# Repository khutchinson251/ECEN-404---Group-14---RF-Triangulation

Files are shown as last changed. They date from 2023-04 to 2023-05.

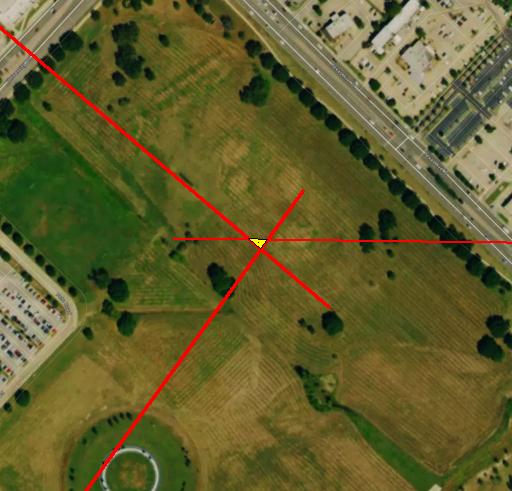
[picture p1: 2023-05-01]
gui/background.jpg

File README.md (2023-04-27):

# ECEN-404-Group-14-RF-Triangulation
ECEN 404 GitHub Repository 

This is for the Texas A&M University Senior Design Class, ECEN 404.
Group 14, RF Triangulation

Our project is based on radio frequency triangulation, where there are three receiving antennas finding one transmitting antenna.
Transmitter have a PCB with a MCU and Radio Module.
Receivers have a PCB with a MCU, Radio Module, and Stepper Motor IC; Stepper Motor; and a 12V battery.

This GitHub will compile all presentations, code, parts, Altium designs, and documentation for the project.

To see the GitHub Repository from ECEN 403, click here: https://github.com/Brandonstokes6/RF-Triangulation

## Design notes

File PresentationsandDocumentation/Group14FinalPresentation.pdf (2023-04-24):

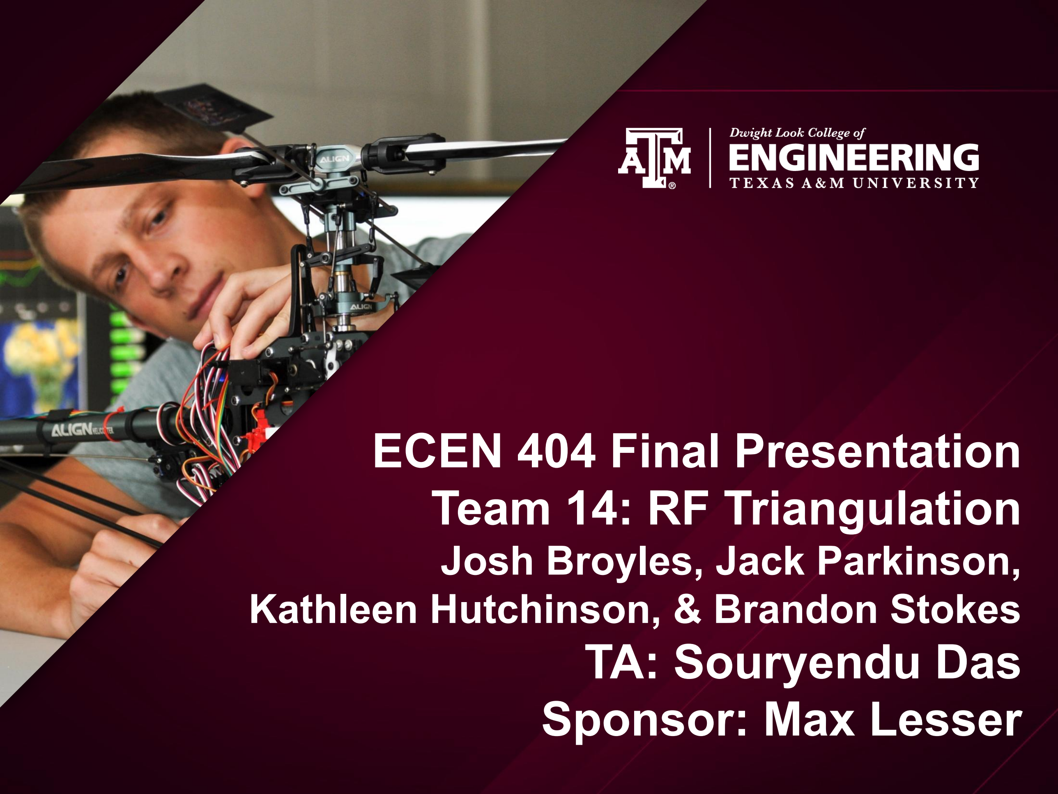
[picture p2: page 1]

# ECEN 404 Final Presentation Team 14: RF Triangulation

Josh Broyles, Jack Parkinson,

## Kathleen Hutchinson, & Brandon Stokes

# TA: Souryendu Das Sponsor: Max Lesser

# Project Summary

Biologists have struggled being able to collect data on wildlife’s location, habitat use, and breeding patterns without getting directly involved with the animal they’re tracking.
Radio Frequency Triangulation
allows a user to track a known
frequency (such as a previously tagged animal) within the
triangulated area of three antennas by using a motor to successfully pinpoint the
strongest signal.

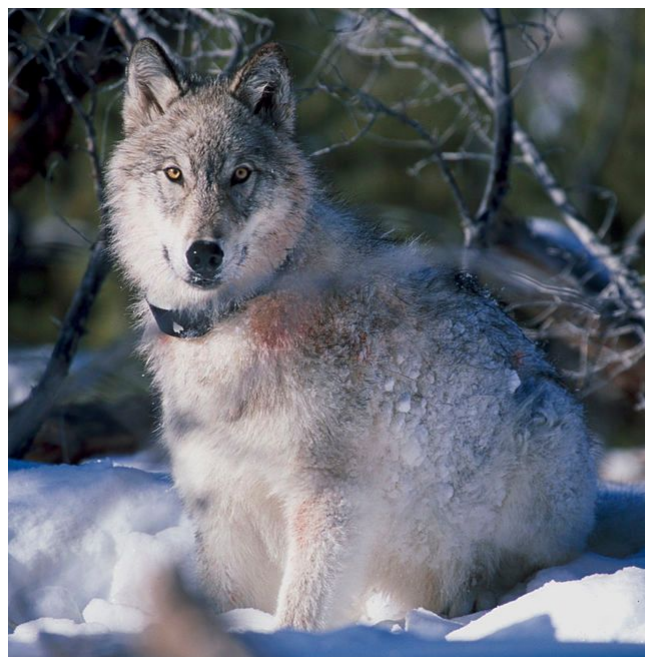
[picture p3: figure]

Helpful to study both invasive and threatened wildlife, our RF Triangulation system will focus on being able to accurately track a transmitter within a 100 meter radius with >10% error.

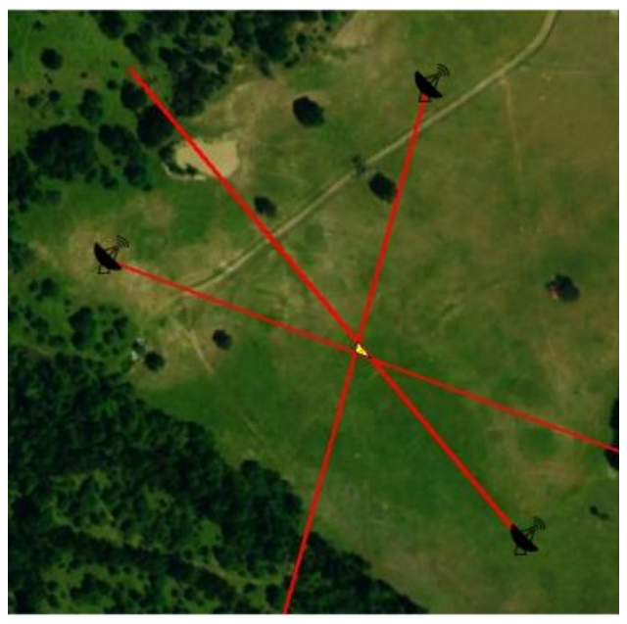
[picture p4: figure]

## Integrated Project Diagram

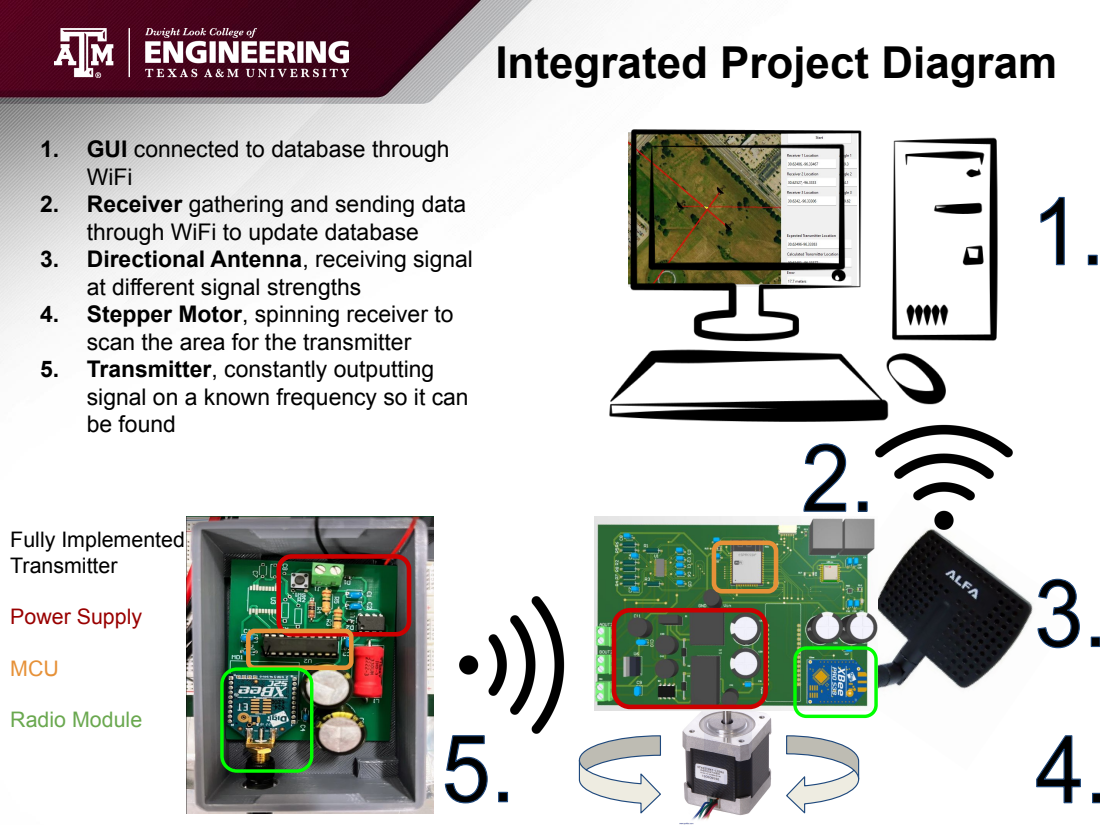
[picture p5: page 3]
Fully Implemented Transmitter; Power Supply; MCU; Radio Module

1. GUI connected to database through
WiFi
2. Receiver gathering and sending data
through WiFi to update database
3. Directional Antenna, receiving signal
at different signal strengths
4. Stepper Motor, spinning receiver to
scan the area for the transmitter
5. Transmitter, constantly outputting
signal on a known frequency so it can
be found

## Josh Broyles Accomplishments

Designed | Tested | Challenges | Solutions

PCB Designed:
- MSP430
- Xbee
- Ublox

Coded
- MSP430
- Transmit
- Echo
- Xbee

PCB:
- Power Supply
- Line Regulation
- Load Regulation

Code:
- MSP430 Transmit
message to Xbee
- MSP430 Echo
message back
through Xbee

Other:
- Transmitter
Range Test
- MSP430
unresponsive I2C
commands
- MSP430
debugging without
terminal
- MSP430 reset
does not rerun
program
- GPS
coordinates can
be hardcoded in
- MSP can output
messages to
Xbee, which can
be used to
debug
- Turning the
system off then
back on will
rerun the
program

## Josh Broyles Designed / Coded

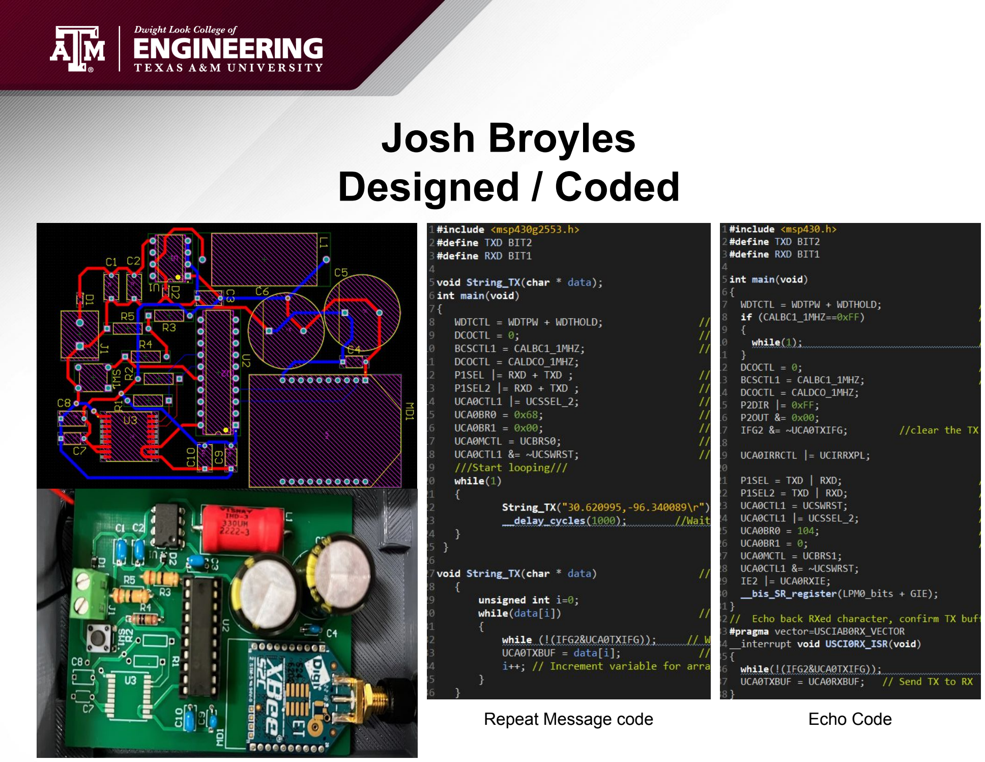
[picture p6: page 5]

Repeat Message code | Echo Code

## Josh Broyles Validation

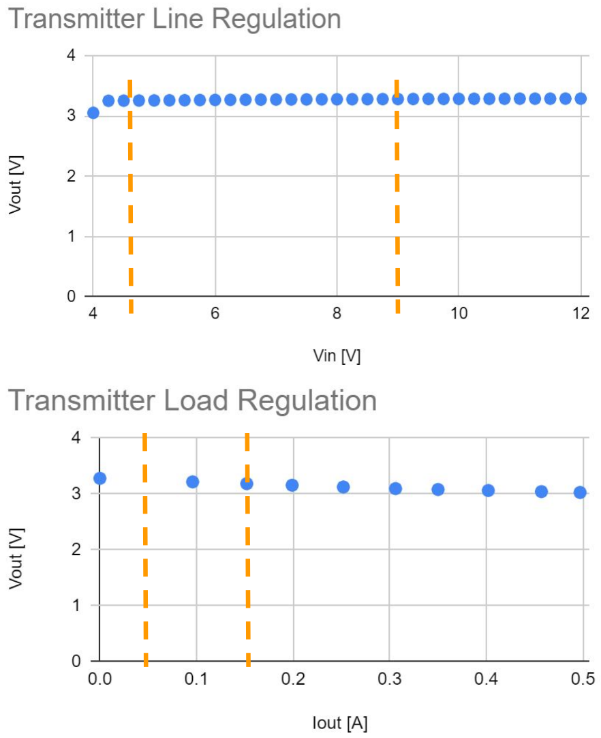
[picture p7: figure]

Requirement | Validated
Vout = 3V - 3.3V with Vin between 4.5V - 9V | Vin = 9V, Vout = 3.281V Vin = 4.5V, Vout = 3.25V
3V - 3.3V at 0.15A for MCU and other modules | 3.182V at 0.152A

## Jack Parkinson Accomplishments

Designed | Tested | Challenges | Solutions

PCB Design:
- Stepper Motor
Driver
- 12V regulator

Directional Antenna:
- Patch Antenna
- Yagi Antenna

ESP32 Stepper
Motor Code

PCB:
- 12V regulator

Directional Antenna:
- directionality
- range

Stepper Motor:
- speed
- step size
- step direction
- motor torque
- ESP32 flash
capabilities
- Motor Driver
parts too small
- 12V regulator
dropout voltage
too large
- Patch Antenna
simulation
- Yagi antenna
manufacturing
- Redesign
PCB
- Buy new parts
- Buy an
antenna

## Jack Parkinson Tested

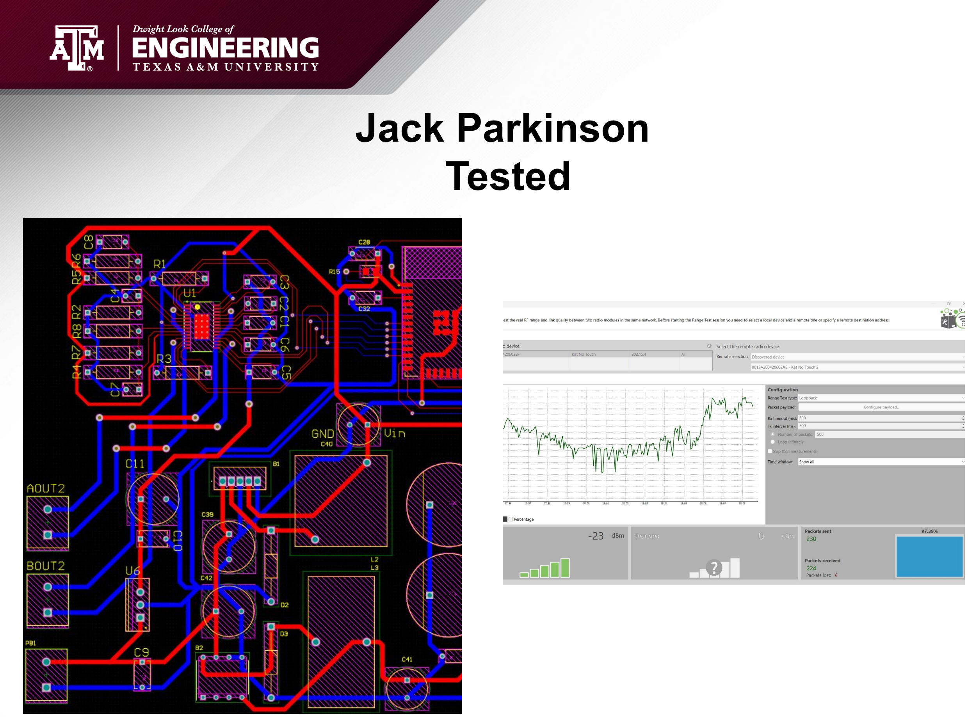
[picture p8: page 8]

## Kathleen Hutchinson Accomplishments

Designed | Tested | Challenges | Solutions

PCB Designed:
- ESP32
- XBee
- GPS
- Magnetometer
- Pycom

Coded
- ESP32
- XBee
- Pycom

PCB:
- Power Supply
- ESP32 Tx0/Rx0

Code:
- ESP32 reading
XBee data
- ESP32 reading
and transmitting
Pycom data
Other:
- XBee Accuracy
- Transmission Time
- SPI and I2C with
small, surface
mount modules
- Circuit/PCB
design
- XBee RSSI value
- XBee accuracy
(packets) drop
after 50 meters
- Power Supply
(inductors,
heating problems)

GPS Coordinates
can be manually
set since phone
hotspots will be
used

Power supply and
connections are
updated on new
PCB

## Kathleen Hutchinson Designed / Coded

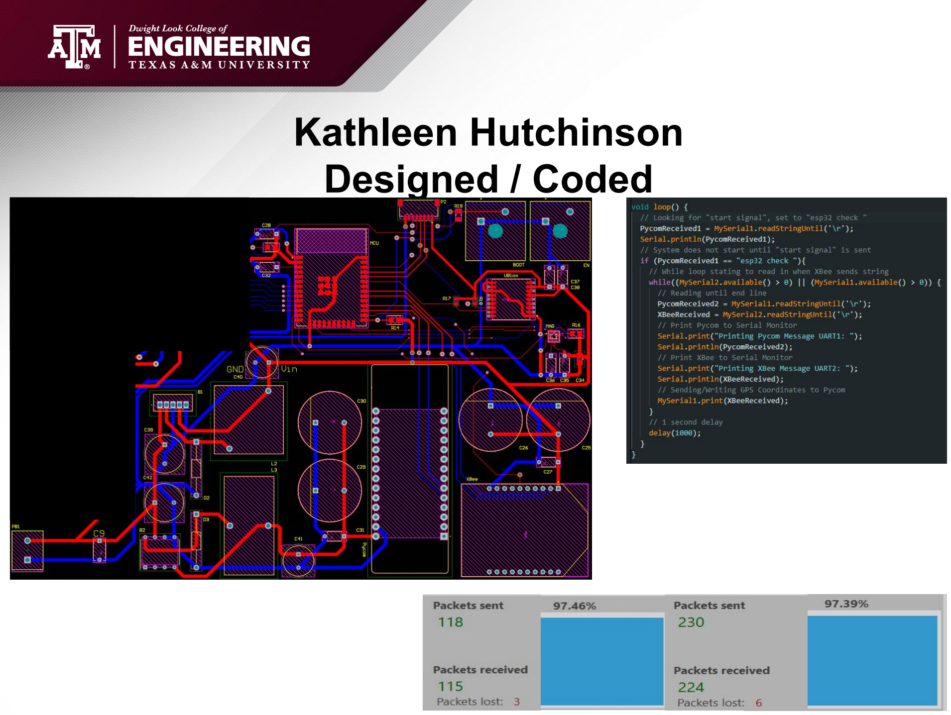
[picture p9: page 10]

## Kathleen Hutchinson Validation

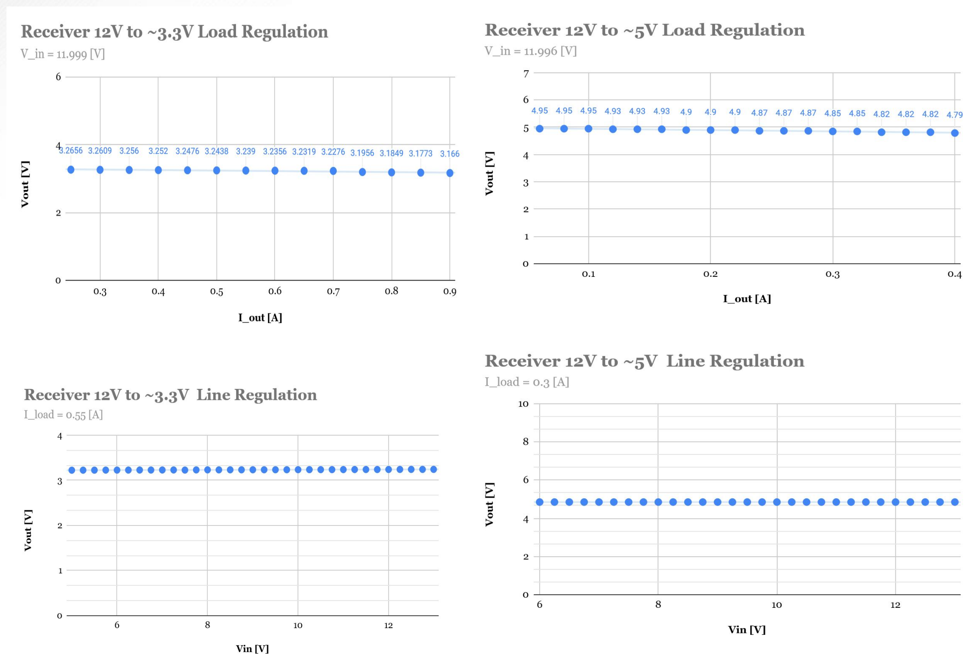
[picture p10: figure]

Requirement | Validated
3V at 1A for modules & MCU | 3.1V at 1A
3.5V at 0.5A for Pycom | 4.7V at 0.5A
30 sec transmission time | ~14 sec transmission time

## Brandon Stokes Accomplishments

Designed | Tested | Challenges | Solutions

GUI Designed:
- Display locations
based on GPS
- Satellite map view
of the area
- Error between the
calculated and
actual transmitter
Database:
- Hosted on AWS that
stores all the
relevant information
Pycom:
- Coded communication
between GUI,
Database and MCU

WiFi:
- WiFi connection
will be able to run
continuously for 20
minutes and be
able to reconnect
Code:
- Gives errors for wrong
values(i.e given a
wrong angle will tell
you which receiver it
came from
- How much RAM the
program takes up on
Users computer
Other:
- Database integrity
to not allow
duplicate values for
receiver data
- LTE | Solution to not having LTE was to use WiFi hotspots as the connection for each of the receivers

## Brandon Stokes Design

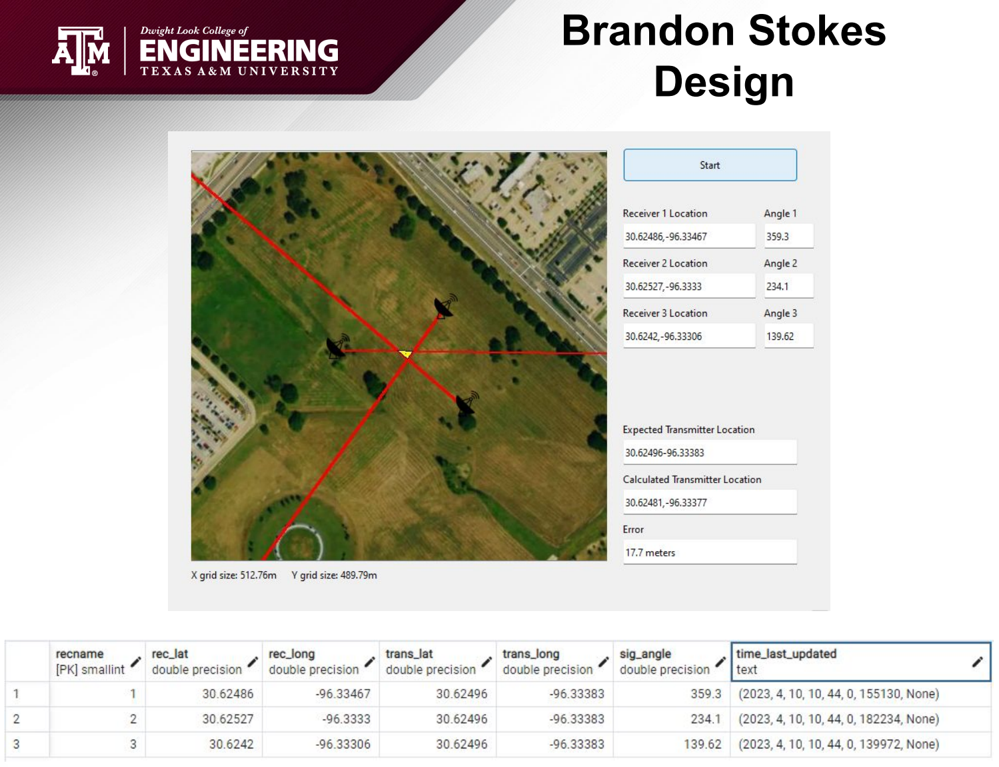
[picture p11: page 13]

## Brandon Stokes Validated

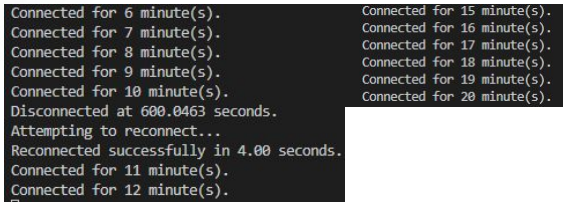
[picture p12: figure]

Requirement

The wifi hotspot does not drop more than 1 time per 5 minutes
and shall reconnect within 20s.

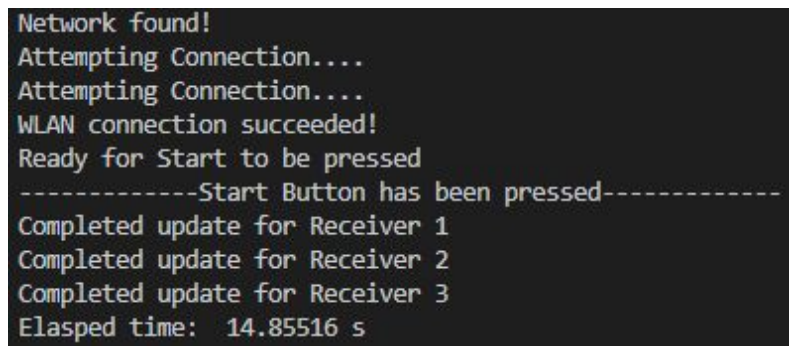
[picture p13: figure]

Total Pycom connection time max = 20 min

The time it takes to connect and transmit data between the GUI, transmitter, and receiver shall be 30s.

The GUI shall not take up more than 1 GB RAM on user's computer.

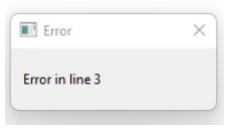
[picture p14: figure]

The Database should not be able to take in duplicate values or
values that do not match the expected criteria

# Integrated System Results

The connection between the transmitting XBEE and the receiver’s XBEE, ESP32, Pycom, to database transmits in about 14 seconds, as previously stated in Brandon Stokes’s slide.

When within about 50 meters of each other, the XBEE’s have an accuracy of 97%; however, our project requires a distance of 100 meters from each antenna - thus an updated antenna is required.

Performance will be improved with a redesigned PCB.

Success in this area was described as successfully transmitting data, failure would be a lack of communication.

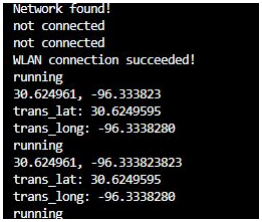
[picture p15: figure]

Further system success criteria requires the motor and redesigned PCB
to successfully move to find the transmitter.

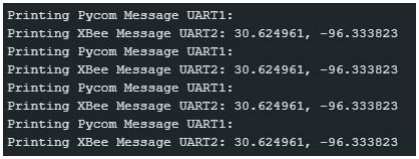
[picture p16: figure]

# Conclusions

Some parts of the project were changed due to changes in the modules. Specifically, the major changes resulted in the project moving from:
- Automatically reading in GPS coordinates from the UBLOX module to | manually
entering the coordinates | because the team was unsuccessful in reading the data.
- Using the magnetometer to move system to North to | manually setting the | receivers
facing North when placed in the field.
- Using LTE through the Pycom module because the module refused to connect with multiple sim cards, thus the team switched to WiFi hotspots.

Current Status

Transmitter | Fully Tested/Validated
Antenna and ESP32+Modules | Repeating Testing for Replacement PCB
Motor and ESP32+Modules | Repeating Testing for Replacement PCB
Pycom and ESP32+Modules | Repeating Testing for Replacement PCB
GUI + Database and Pycom | Fully Integrated/Tested/Validated

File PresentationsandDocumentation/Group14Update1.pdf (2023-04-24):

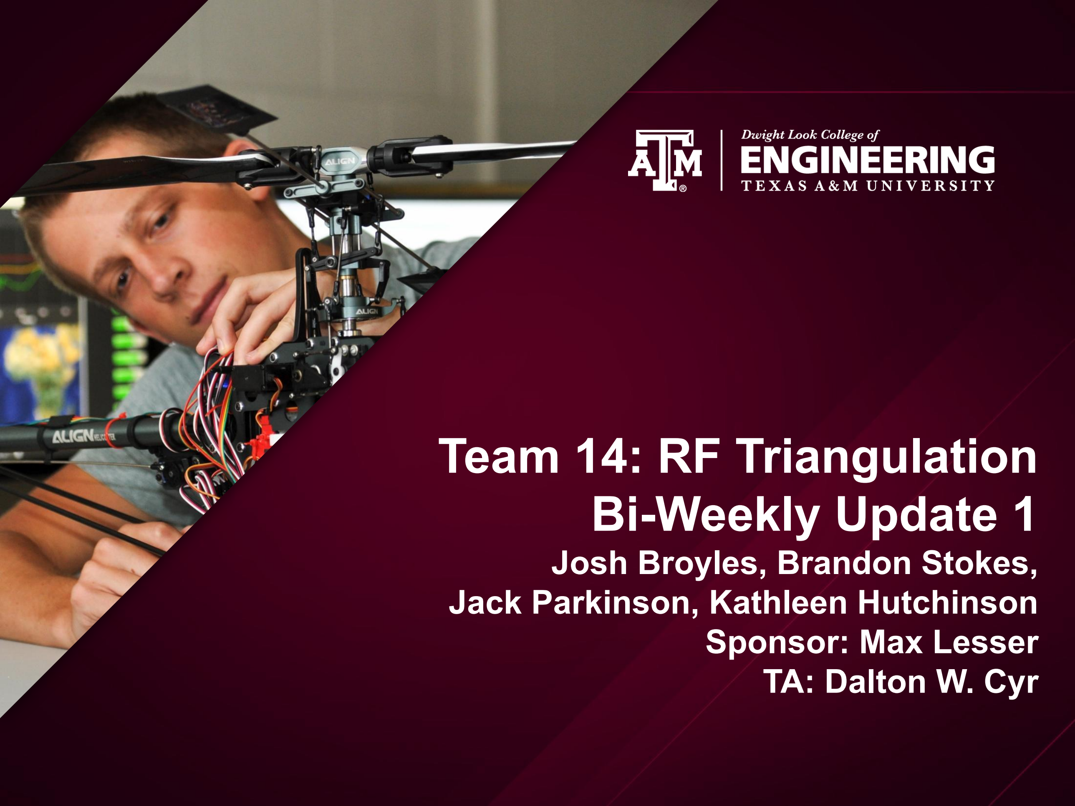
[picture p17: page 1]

# Team 14: RF Triangulation Bi-Weekly Update 1

Josh Broyles, Brandon Stokes,

### Jack Parkinson, Kathleen Hutchinson Sponsor: Max Lesser TA: Dalton W. Cyr

# Project Summary

This project utilizes three receivers with motors to scan an area for the

strongest radio frequency signal from the transmitter and use their

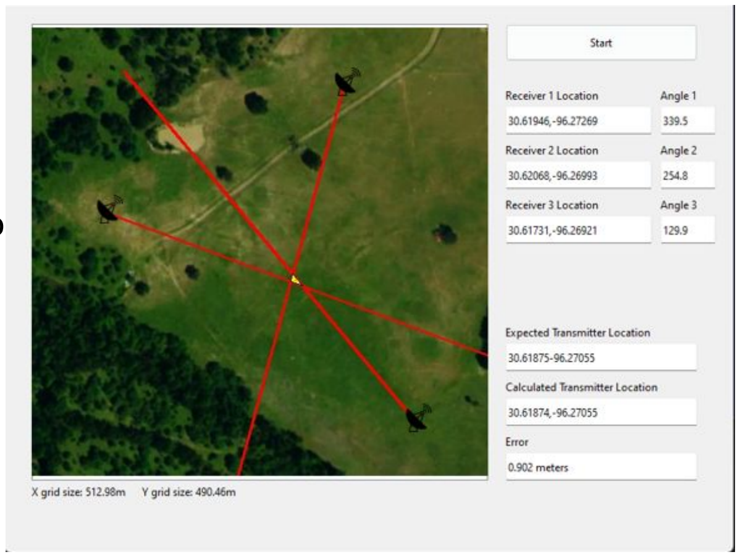
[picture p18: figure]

collective angles from “true” North to determine the location of the transmitter.

Then, the GUI will display this information to the user.

## RF Triangulation deals with determining the random

location of a transmitter in an 100 meter area.

# Project/Subsystem Overview

Josh Broyles - Transmitter
- PCB design for Transmitter
- Programming Transmitter MCU
- Sends out Radio Frequency

Jack P. - Receiver - Antenna/Motor
- PCB design for motor driver
- Programming ESP32 for motor
- Receives signal

Kathleen H. - Receiver - ESP32 Modules
- PCB design for ESP32 and 4 modules
- Programming ESP32 for modules
- Sends signal to Database

Brandon Stokes - Database & GUI
- Database creation
- Display of transmitter location to User
- Error calculation through GPS

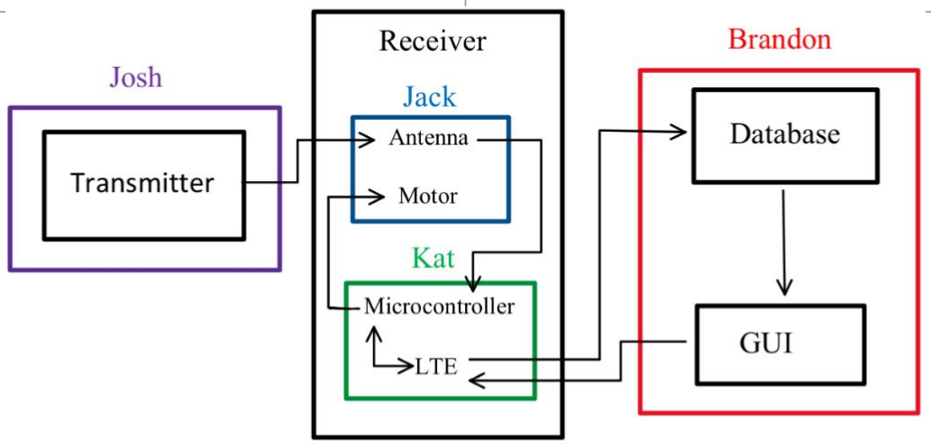
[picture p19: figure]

# Major Project Changes for 404

Original Goal:
Search area of minimum 500 meters
Now:
Due to the higher frequency of the XBEE’s used, the maximum distance will now be 100m

Original Subsystems:
Kathleen had been tasked with programming the Pycom (LTE Module) for the database connection
Now:
Brandon will take over programming the Pycom (LTE Module)

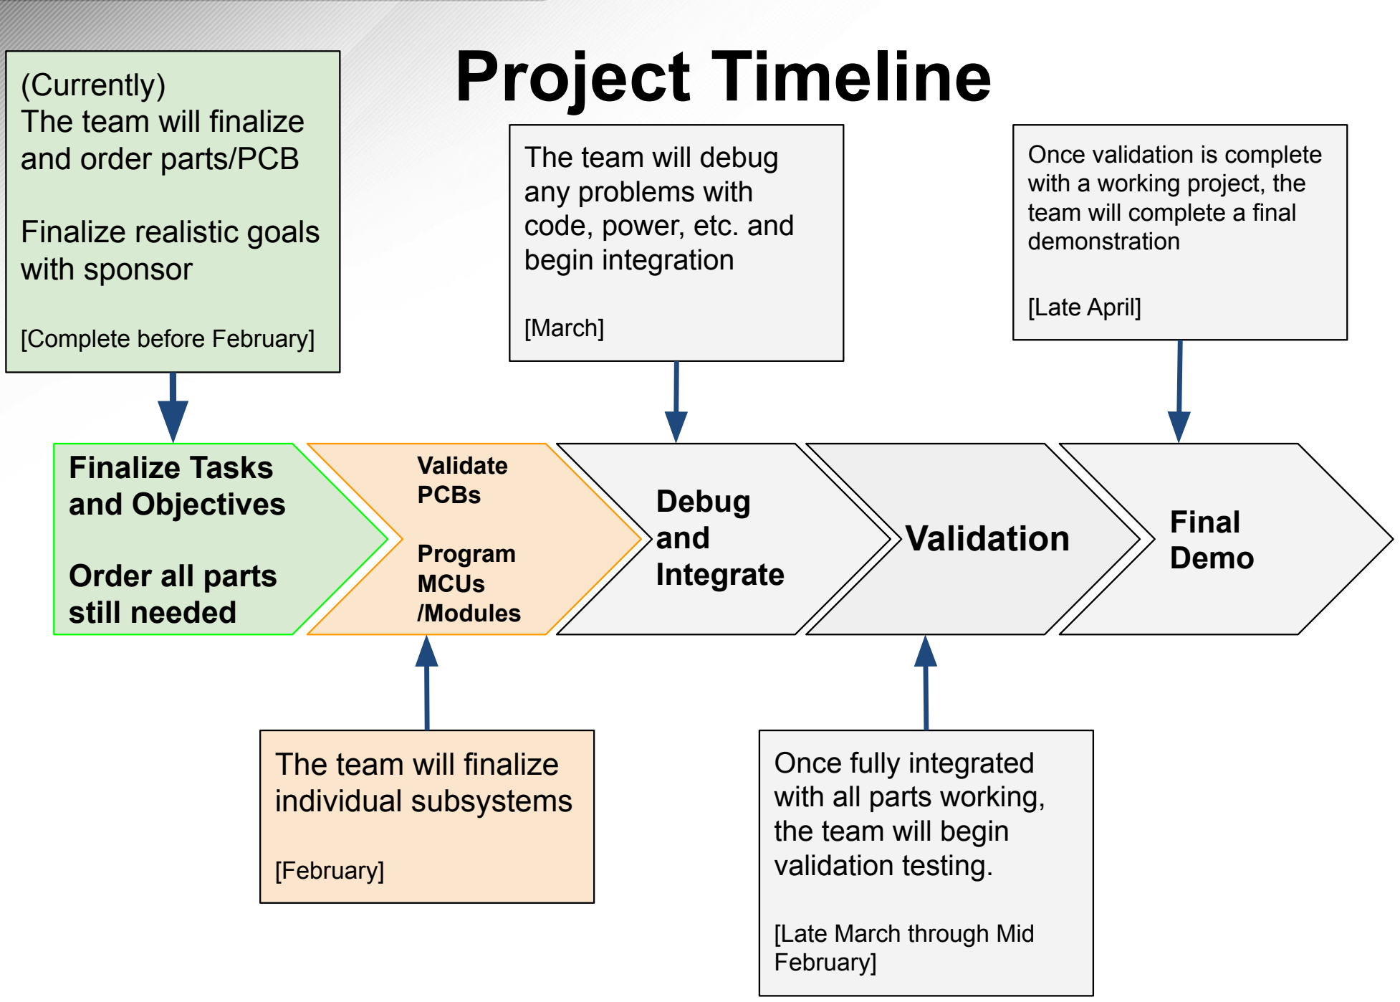
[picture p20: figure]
Project Timeline; Validate PCBs; Program MCUs /Modules; Finalize Tasks and Objectives; Order all parts still needed; Final Demo Validation; Debug and Integrate; (Currently) The team will finalize and order parts/PCB; Finalize realistic goals with sponsor; [Complete before February]; The team will finalize individual subsystems; [February]; The team will debug any problems with code, power, etc. and begin integration; [March]; Once fully integrated with all parts working, the team will begin validation testing.; [Late March through Mid February]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

# Transmitter

Josh Broyles

Accomplishments since 403
14 hrs of effort

Ongoing progress/problems and plans until the next presentation

PCB fabricated

PCB rung out and validated

Radio communication established

Radio distance test (reaches up to 150m)

Set up GPS on PCB

Update MCU code for GPS input

# Transmitter

Josh Broyles

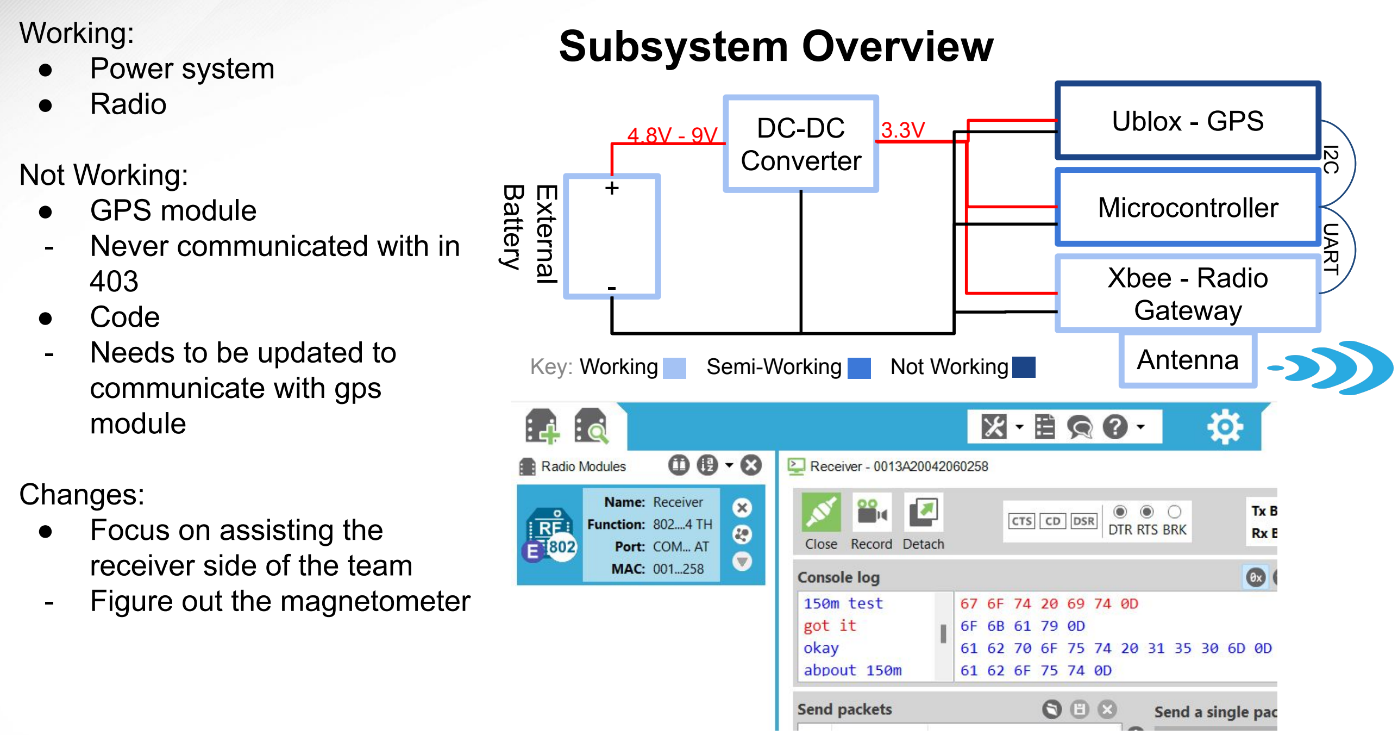
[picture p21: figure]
DC-DC Converter; Battery; External; Ublox - GPS; Microcontroller; Xbee - Radio Gateway; UART I2C; Subsystem Overview; Antenna; Working: ● Power system ● Radio; Not Working: ● GPS module - Never communicated with in 403 ● Code - Needs to be updated to communicate with gps module; Changes: ● Focus on assisting the receiver side of the team - Figure out the magnetometer; Key: Working; Semi-Working; Not Working

# Receiver: Antenna & Motor

Jack Parkinson

Accomplishments since 403
12hrs of Effort

Ongoing progress/problems and plans until the next presentation Made a contingency plan with sponsor for the future of the antenna

1. Working on antenna simulation

and design

2. Helping with PCB finalization
3. Continue working on code to

control the motor

# Receiver: Antenna & Motor

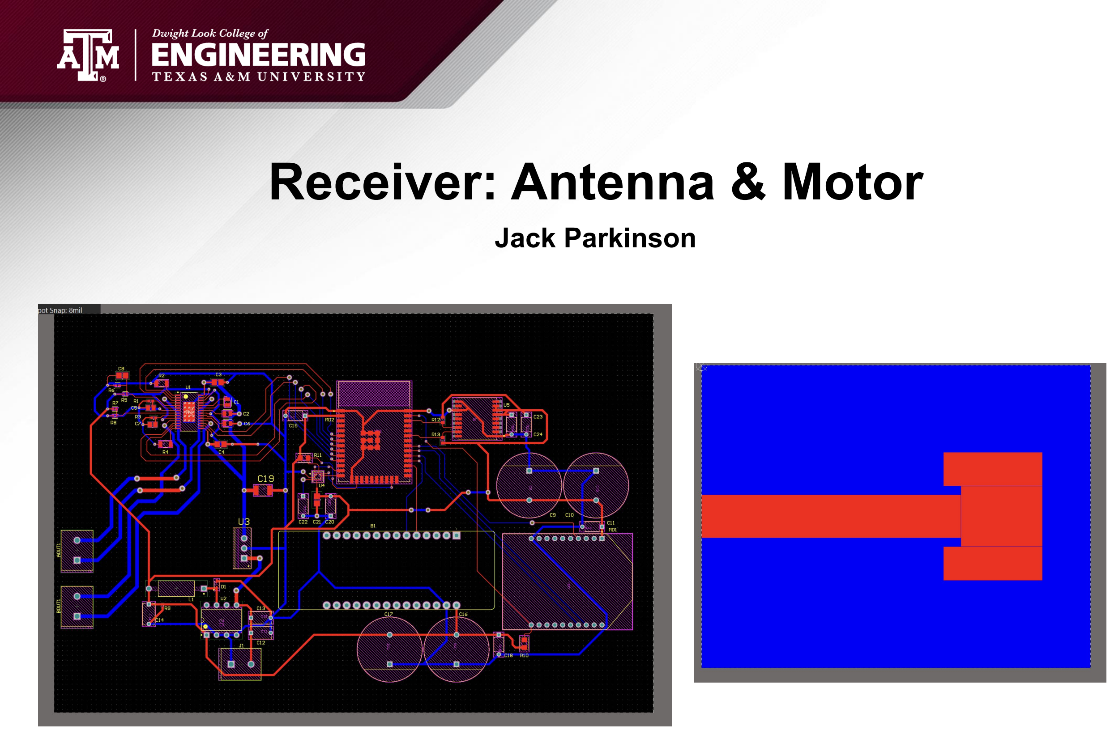
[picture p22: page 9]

Jack Parkinson

Interesting figure related to your subsystem
progress

Detail on what works,
what doesn’t, what is
changing

# Receiver: ESP32 & Modules

Kathleen Hutchinson

Accomplishments since 403
15 hrs of effort

Ongoing progress/problems and plans until the next presentation

Radio distance test (reaches up to 150m)

New Schematic for Receiver
(due to change in PCB Design discussed with Dr. Lusher)
1. PCB Design Finalization &

confirm with Dr. Lusher

2. Order PCB & required parts
3. Continue to program ESP32 for

XBee & verify (while waiting for PCB

to be printed)
4. Work with Brandon on LTE

## Receiver: ESP32 & Modules

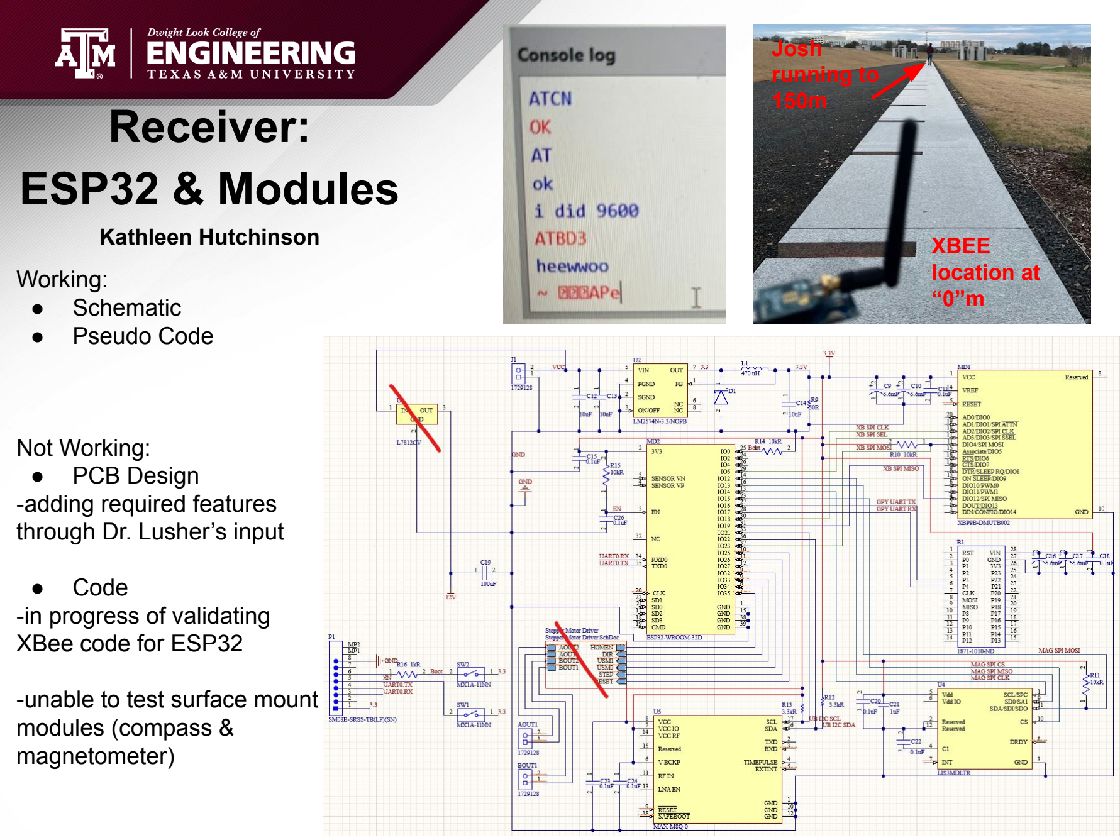
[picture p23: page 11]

Kathleen Hutchinson

Working: ● | Schematic ● | Pseudo Code
Not Working: ● | PCB Design

-adding required features
through Dr. Lusher’s input ● Code

-in progress of validating XBee code for ESP32

-unable to test surface mount modules (compass &
magnetometer)

Josh
running to
150m

XBEE
location at
“0”m

# Database & GUI

Brandon Stokes

Accomplishments since 403
15 hrs of effort

Ongoing progress/problems and plans until the next presentation Added some extra functionality to allow the receivers data to come in at different times

-Data Validation to ensure data is correct before beginning process -Rework the database schema to handle successive runs
-General error checking to pinpoint if one receiver is not incorrect
-Fixing where you do not need to press start again if its outside the bound

# Database & GUI

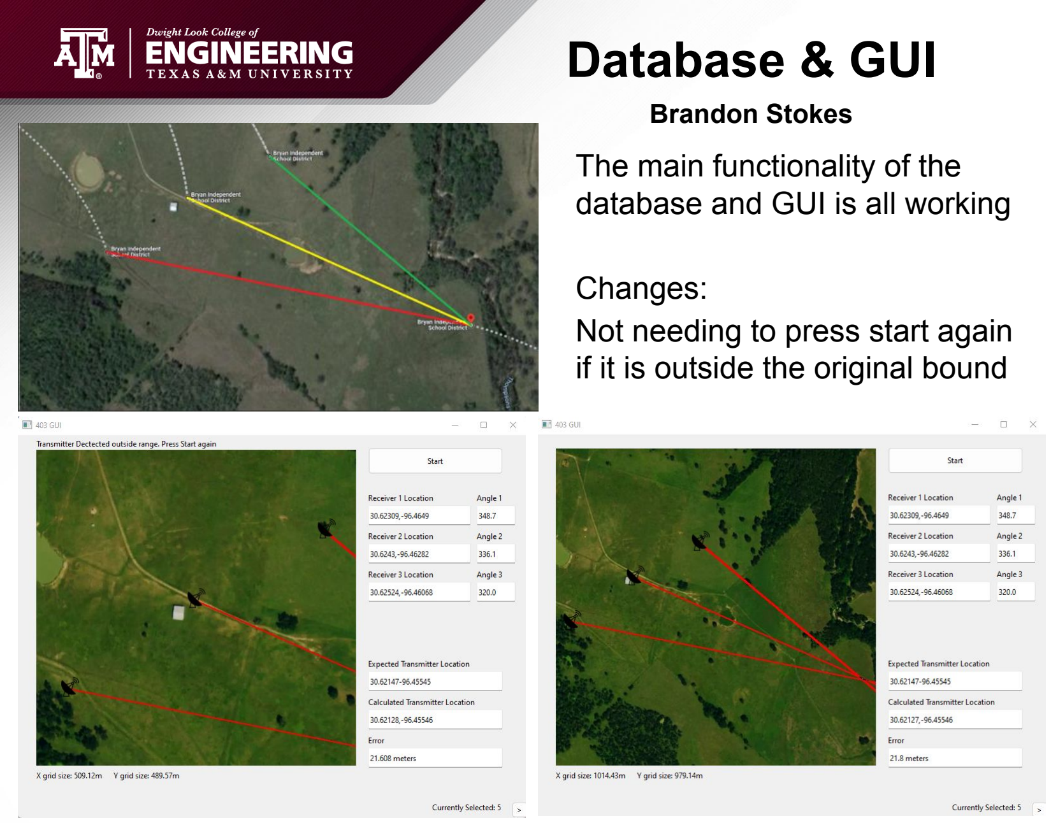
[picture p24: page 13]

The main functionality of the database and GUI is all working

Changes:
Not needing to press start again if it is outside the original bound

Brandon Stokes

# Parts Ordering Status

Transmitter:
- All parts received, including printed PCB

Receiver:
ESP32/Modules
- Informed recently from Dr. Lusher that PCB design was missing parts
- Parts will be ordered within the week:
■ New Inductor
■ More Resistors
■ Push Buttons
■ USB Connector
■ LTE Antenna & Chip
■ Stepper Motor Controller IC
- PCB will be ordered within the week

Antenna:
- Antenna Design is still being worked on but should be ordered by next week

# Execution & Plan

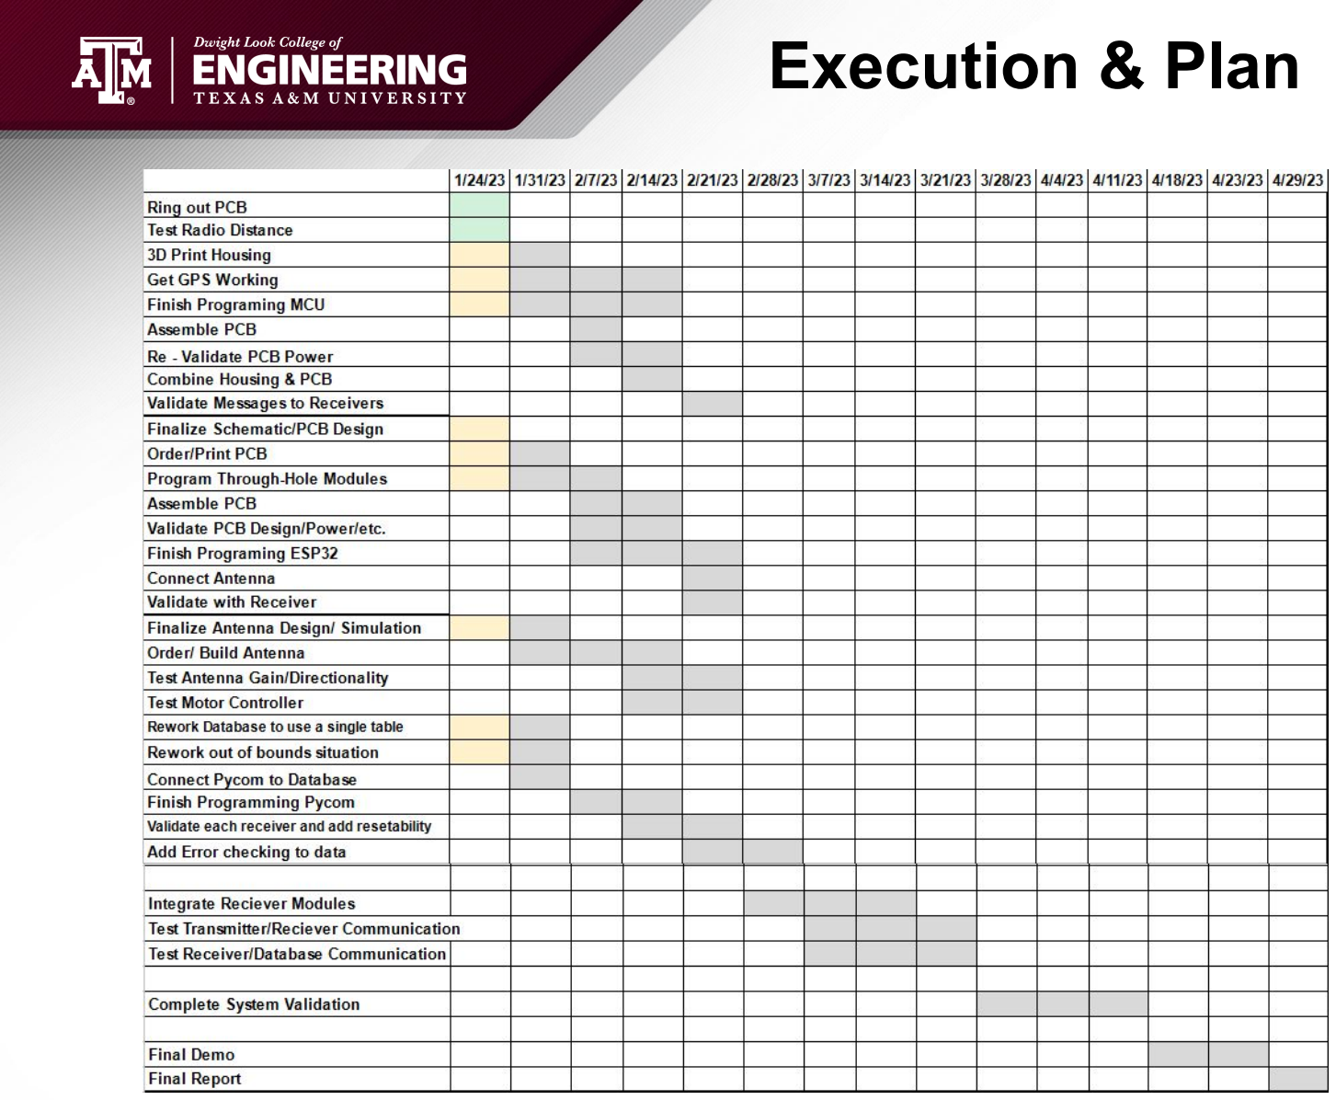
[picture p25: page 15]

# Thank you for your attention!

# Feel free to ask us questions

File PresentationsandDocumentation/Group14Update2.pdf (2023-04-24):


# Team 14: RF Triangulation Bi-Weekly Update 2

Josh Broyles, Brandon Stokes,

### Jack Parkinson, Kathleen Hutchinson

### Sponsor: Max Lesser TA: Souryendu Das

# Project Summary

## How do you accurately find a signal source in a ~100 meter area?


RF Triangulation uses three
receivers with motors to scan an area for the strongest radio frequency signal from the
transmitter and use their
collective angles from “true” North to determine the location of the transmitter.

## Within ~10% error

(currently calculating <5%)

# Project/Subsystem Overview

Josh Broyles - Transmitter
- PCB design for Transmitter
- Programming Transmitter MCU
- Sends out Radio Frequency

Jack P. - Receiver - Antenna/Motor
- PCB design for motor driver
- Programming ESP32 for motor
- Receives signal

Kathleen H. - Receiver - ESP32 Modules
- PCB design for ESP32 and 4 modules
- Programming ESP32 for modules
- Sends signal to Database

Brandon Stokes - Database & GUI
- Database creation
- Display of transmitter location to User
- Error calculation through GPS


Project Timeline; Validate PCBs; Program MCUs /Modules; Finalize Tasks and Objectives; Order all parts still needed; Final Demo Validation; Debug and Integrate; The team will finalize and order parts/PCB; Finalize realistic goals with sponsor; [Complete before February]; The team will finalize individual subsystems; [February]; The team will debug any problems with code, power, etc. and begin integration; [March]; Once fully integrated with all parts working, the team will begin validation testing.; [Late March through Mid April]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

# Transmitter

Josh Broyles

Accomplishments since 404
16 hrs of effort

Ongoing progress/problems and plans until the next presentation

3D Printed Radio Housing

Tested GPS module, confirmed it is in standby mode

Re-wrote MCU to interface with GPS

On-going test of GPS accuracy

Begin soldering PCB together

# Transmitter


Josh Broyles

Accomplishments since 404
18 hours

Ongoing progress/problems and plans until the next presentation

Final parts list for PCB has been ordered

PCB has been ordered

Antenna design has been decided and created

Simulate the antenna design

Buy parts and assemble antenna in preparation for testing

Assemble PCB

# Receiver: Antenna & Motor

Jack Parkinson

# Receiver: Antenna &


# Motor

Jack Parkinson

Accomplishments since 404
20 hrs of effort

Ongoing progress/problems and plans until the next presentation

Completed ordering parts in preparation for PCB (received today)

PCB Ordered

1. Work on connection between ESP32 and Pycom (UART)
2. Work on connection between ESP32 and XBEE (SPI)

Problems:
Getting RX/TX to send messages between Pycom & ESP32

# Receiver: ESP32 & Modules

Kathleen Hutchinson

## Receiver: ESP32 & Modules


Kathleen Hutchinson

Accomplishments since 404
17 hrs of effort

Ongoing progress/problems and plans until the next presentation

- Fixed out of bounds situation to not need to press start again
- Reworked the database to be a single table to do multiple runs in preparation for integration
- Communicating from the Pycom to Database
- Adding a percentage error instead of raw error
- Problems: Connecting Pycom to my local computer

# Database & GUI

Brandon Stokes

# Database & GUI


Brandon Stokes

# Execution & Plan


# Validation Plan


# Thank you for your attention!

# Feel free to ask us questions

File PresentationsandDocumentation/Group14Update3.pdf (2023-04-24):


# Team 14: RF Triangulation Bi-Weekly Update 3

Josh Broyles, Brandon Stokes,

### Jack Parkinson, Kathleen Hutchinson

### Sponsor: Max Lesser TA: Souryendu Das

# Project Summary

Biologists have struggled being able to collect data on wildlife’s location, habitat use, and breeding patterns without getting directly involved with the animal they’re tracking.
Radio Frequency Triangulation
allows a user to track a known
frequency (such as a previously tagged animal) within the
triangulated area of three antennas by using a motor to successfully pinpoint the
strongest signal.


Helpful to study both invasive and threatened wildlife, our RF Triangulation system will focus on being able to accurately track a transmitter within a 150 meter radius with >10% error.

# Project/Subsystem Overview

Josh Broyles - Transmitter
- PCB design for Transmitter
- Programming Transmitter MCU
- Sends out Radio Frequency

Jack P. - Receiver - Antenna/Motor
- PCB design for motor driver
- Programming ESP32 for motor
- Receives signal

Kathleen H. - Receiver - ESP32 Modules
- PCB design for ESP32 and 4 modules
- Programming ESP32 for modules
- Sends signal to Database

Brandon Stokes - Database & GUI
- Database creation
- LTE and GUI connection
- Error calculation through GPS


Project Timeline; Validate PCBs; Program MCUs /Modules; Finalize Tasks and Objectives; Order all parts still needed; Final Demo Validation; Debug and Integrate; The team will finalize and order parts/PCB; Finalize realistic goals with sponsor; [Complete before February]; The team will finalize individual subsystems; [February]; The team will debug any problems with code, power, etc. and begin integration; [March]; Once fully integrated with all parts working, the team will begin validation testing.; [Late March through Mid April]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

# Transmitter

Josh Broyles

Accomplishments since last update 14 hrs of effort

Ongoing progress/problems and plans until the next presentation

Finished MCU code | On-going PCB Assembly
| Begin Validating Transmitter
| Begin working with GPS on Receiver side
| 3D Print Final Radio Housing design

# Transmitter


Josh Broyles

# Receiver: Antenna & Motor

Jack Parkinson

Accomplishments since last update 16 hrs of effort

Ongoing progress/problems and plans until the next presentation

Simulated Yagi Antenna

Finalized Antenna dimensions

Finalize antenna design (how I am going to build it)

Buy parts for antenna

Help Kat Assemble PCB

Finalize code for stepper motor driver

# Receiver: Antenna & Motor


Jack Parkinson

# Receiver: ESP32 & Modules

Kathleen Hutchinson

Accomplishments since last update 17 hrs of effort | Ongoing progress/problems and plans until the next presentation
PCB has arrived | Solder PCB (today 6-9pm) On-going testing of XBee Create housing for PCB that can be mounted on tripod

# Receiver: ESP32 & Modules


Kathleen Hutchinson

# Database & GUI

Brandon Stokes

Accomplishments since last update 20 hrs of effort | Ongoing progress/problems and plans until the next presentation
- Completed integration of database and Pycom over WiFi with ability to read and update data | ● Transition Pycom to LTE instead of WiFi

# Database & GUI


Brandon Stokes

# Execution & Plan


# Validation Plan


# Thank you for your attention!

# Feel free to ask us questions

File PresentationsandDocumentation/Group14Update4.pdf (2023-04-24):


# Team 14: RF Triangulation Bi-Weekly Update 3

Josh Broyles, Brandon Stokes,

### Jack Parkinson, Kathleen Hutchinson

### Sponsor: Max Lesser TA: Souryendu Das

# Project Summary

Biologists have struggled being able to collect data on wildlife’s location, habitat use, and breeding patterns without getting directly involved with the animal they’re tracking.
Radio Frequency Triangulation
allows a user to track a known
frequency (such as a previously tagged animal) within the
triangulated area of three antennas by using a motor to successfully pinpoint the
strongest signal.


Helpful to study both invasive and threatened wildlife, our RF Triangulation system will focus on being able to accurately track a transmitter within a 150 meter radius with >10% error.


Integrated System Diagram; Power Supply; MCU; Radio Module; and three receivers.; transmitter.; added modules that are essential to the; LTE.; still in progress to be finished.

Ideally, our system will have one transmitter

The figure to the right shows a completed

In the future, three receivers of relatively the same form will be created to connect to the

The only differences between will be three

stepper motor and data transmission through

Due to power supply failure, the receiver is

Project Timeline; Validate PCBs; Program MCUs /Modules; Finalize Tasks and Objectives; Order all parts still needed; Final Demo Validation; Debug and Integrate; The team will finalize and order parts/PCB; Finalize realistic goals with sponsor; [Complete before February]; The team will finalize individual subsystems; [February]; The team will debug any problems with code, power, etc. and begin integration; [March]; Once fully integrated with all parts working, the team will begin validation testing.; [Late March through Mid April]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

# Transmitter

Josh Broyles

Accomplishments since last update 39 hrs of effort | Ongoing progress/problems and plans until the next presentation
Validated Transmitter Power Completed Radio Housing Working signal transmission to receiver side | N/A

# Transmitter


Josh Broyles

# Receiver: Antenna & Motor

Jack Parkinson

Accomplishments since last update 26 hrs of effort

Ongoing progress/problems and plans until the next presentation

Finalized Antenna Design

Got Blinky code working on an offboard ESP32

Soldered on about half the PCB for testing

Write code for stepper motor based off of the blinky code

Get red badge

Buy parts for antenna

Help Kat with the PCB problems and integration between our systems

# Receiver: ESP32 & Modules

Kathleen Hutchinson

Accomplishments since last update 39 hrs of effort

Ongoing progress/problems and plans until the next presentation Failed power validation

Connected Josh’s XBEE,
to my XBEE,
through ESP32,
onto Pycom to Brandon

Buying parts
PCB design part 2

Problems:
buck converter
inductor
XBee output

## Receiver: ESP32 & Modules


Kathleen Hutchinson

# Database & GUI

Brandon Stokes

Accomplishments since last update 21 hrs of effort

Ongoing progress/problems and plans until the next presentation
- Completed integration with Kathleen and the
communication between our
systems
- Tested app error handling for receiver off angle and location
- Continue to work with
transitioning from WiFi to LTE

# Database & GUI


Brandon Stokes


## Execution Plan


# Validation Plan


# Thank you for your attention!

# Feel free to ask us questions

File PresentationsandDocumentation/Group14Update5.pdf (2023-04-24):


# Team 14: RF Triangulation Bi-Weekly Update 5

Josh Broyles, Brandon Stokes,

### Jack Parkinson, Kathleen Hutchinson

### Sponsor: Max Lesser TA: Souryendu Das

# Project Summary

Biologists have struggled being able to collect data on wildlife’s location, habitat use, and breeding patterns without getting directly involved with the animal they’re tracking.
Radio Frequency Triangulation
allows a user to track a known
frequency (such as a previously tagged animal) within the
triangulated area of three antennas by using a motor to successfully pinpoint the
strongest signal.


Helpful to study both invasive and threatened wildlife, our RF Triangulation system will focus on being able to accurately track a transmitter within a 150 meter radius with >10% error.


Integrated System Diagram; Power Supply; MCU; Radio Module; and three receivers.; transmitter.; added modules that are essential to the; LTE.; still in progress to be finished.

Ideally, our system will have one transmitter

The figure to the right shows a completed

In the future, three receivers of relatively the same form will be created to connect to the

The only differences between will be three

stepper motor and data transmission through

Due to power supply failure, the receiver is

Project Timeline; Validate PCBs; Program MCUs /Modules; Finalize Tasks and Objectives; Order all parts still needed; Final Demo Validation; Debug and Integrate; The team will finalize and order parts/PCB; Finalize realistic goals with sponsor; [Complete before February]; The team will finalize individual subsystems; [February]; The team will debug any problems with code, power, etc. and begin integration; [March]; Once fully integrated with all parts working, the team will begin validation testing.; [Late March through Mid April]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

# Brandon Stokes

Accomplishments since last update 16 hrs of effort | Ongoing progress/problems and plans until the next presentation
-Validated being able to lose signal and reconnect on WiFi -Validated timing test for sending from Receiver to Database | -Final attempt at LTE -Develop more validation scenarios for GUI

# Brandon Stokes


# Kathleen Hutchinson

Accomplishments since last update 25 hrs of effort

Ongoing progress/problems and plans until the next presentation

Validated power supply for
- 12V to 3.3V
- 12V to 5V

Validated time to transfer data to database (with Brandon)

Finished 2nd PCB version with:
- new buck converters
- new UART from XBEE to
ESP32

Ongoing ESP32 validation with magnetometer & GPS

Ongoing XBEE validation with RSSI value

Ongoing PCB/Parts ordering

# Kathleen Hutchinson


# Jack Parkinson

Accomplishments since last update 25 hrs of effort

Ongoing progress/problems and plans until the next presentation

Purchased Antenna

Stepper motor control code flashed on to MCU and tested off board

New 12V regulator with smaller dropout voltage chosen

Validated new 12V to 5V converter

Test the antenna with the Xbee’s

MCU code integration with Kat

Test Motors torque and functionality with Max

Finalize last PCB design and order all associated new parts

# Jack Parkinson


# Josh Broyles

Accomplishments since last update 24 hrs of effort | Ongoing progress/problems and plans until the next presentation
Acquired parts needed for Receiver Power Validated power supply for ● 12V to 5V | Validate system distance with directional antenna Develop battery lifetime system test for transmitter

## Execution Plan


# Validation Plan


# Thank you for your attention!

# Feel free to ask us questions

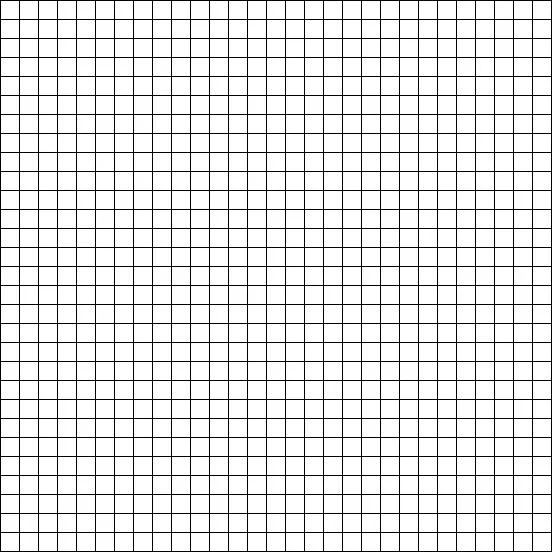
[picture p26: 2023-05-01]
gui/5h0rzl7bzf241.webp

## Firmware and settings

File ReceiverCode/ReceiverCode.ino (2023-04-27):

//Includes
#include <stdio.h>
#include "freertos/FreeRTOS.h"
#include "freertos/task.h"
#include "driver/gpio.h"
#include "esp_log.h"
#include "sdkconfig.h"
// for UART
#include <HardwareSerial.h>
#include <Arduino.h>

//Defines
//Stepper Motor Driver GPIO pin asssignments
#define STEP_GPIO  GPIO_NUM_26
#define DIR_GPIO  GPIO_NUM_27
#define RESET_GPIO  GPIO_NUM_25
#define HOMEN_GPIO  GPIO_NUM_35
#define USM0_GPIO  GPIO_NUM_32
#define USM1_GPIO  GPIO_NUM_33
// GPIO Assignements for UART
#define RX1       GPIO_NUM_16 //to pycoom gpio15
#define TX1       GPIO_NUM_17 //to pycom gpio4
#define RX2       GPIO_NUM_18 //to XBEE Tx=pin2
#define TX2       GPIO_NUM_19 //to XBEE Rx=pin3 

//Set for how long the antenna should wait in a position to get the RSSI value
#define RSSI_WAIT_TIME 5000

//Set the size of sweep around pole and how many points to check within that sweep
#define SWEEP_ANGLE 90
#define SWEEP_STEP_COUNT 10

// UART1, to Pycom
HardwareSerial MySerial1(1);
// UART2, to XBEE
HardwareSerial MySerial2(2); 

// Storing certain messages for UART
String PycomReceived1; 
String PycomReceived2;
// Specifically the XBEE sends out the GPS Coordinates
// of the TRANSMITTER
String XBeeReceived; 
// This states which receiver is transmitting data
// used for Pycom->Database
String ReceiverName;

/*
  The XBEE's were determined to have not enough directional RSSI; we
  tried 3 different antennas, 1 omnidirectional and 2 directional,
  and could not accurately determine the location of the transmitter in 
  the short AND long range tests. Because of this, we have created a 
  dictionary that will take the ideal angle of the receiver 
  of the given transmitter GPS coordinates and determine this to have the 
  strongest, ideal RSSI value of 0. Then, from there, as the receiver sweeps,
  a RSSI value corresponds to the angle checked, creating a triangle-like
  area of RSSI, where 0 is the peak and the most ideal angle. 

  Please note that this was made clear to the demo TA. RSSI was 
  attempted many, many times and unable to be used with the XBEE's.
*/
//Creating a struct to make the dictionary of key and values
struct KeyValuePair {
  float key;
  int value;
}
// 360 / 0.225 + 1 for Dictionary size
const int DICT_SIZE = 1601; 

//This is the case for when the angle given is negative it to make it the corresponding positive value
float validateKey(float keyValue) {
  if (keyValue < 0) {
    keyValue += 360;
  }
  return keyValue;
}
//Had to add in this function to make it so it wraps around to have the same value at 0 as it does 360 for the purpose
//Of having a key at 356 that it would be close to 0 when checking the poles
int wrappedDistance(float peakKeyValue, float angle) {
  int directDistance = abs(peakKeyValue - angle);
  int wrappedDistance = 360 - directDistance;
  return min(directDistance, wrappedDistance);
}

//Creating the dictionary using an absolute value function where we are able to choose where the intercept was
void createRevAbsDict(float peakKeyValue, KeyValuePair* revAbsDict) {
  float step = 0.225;

  for (int i = 0; i < DICT_SIZE; i++) {
    float angle = i * step;
    angle = validateKey(angle);
    revAbsDict[i].key = angle;

    int distance = wrappedDistance(peakKeyValue, angle);
    revAbsDict[i].value = distance;
  }
}

//Getting the value for this specific key, this is used in place for the get_rssi() function to get the
//corresponding rssi for an angle
int getValueForKey(float key, KeyValuePair* revAbsDict) {
  key = validateKey(key);
  const float epsilon = 0.001;

  for (int i = 0; i < DICT_SIZE; i++) {
    if (abs(revAbsDict[i].key - key) < epsilon) {
      return revAbsDict[i].value;
    }
  }

  return -1; // Return -1 if the key is not found
}

int get_rssi() {
    long randnum;
    randnum = random(20,51);
    int random_number = (int)randnum;
    return random_number; 
}



void step(bool step_direction, int step_speed, bool USM0, bool USM1) {

    /* Step function instructions

    direction
        1 => clockwise
        0 => counter_clockwise
    
    speed
        ms per period

    size
        00  => full step
        01  => half step
        10  => quarter step
        11  => eighth step
    
    */


    //Set delay based on period
    int pulse = step_speed / 2;

    //Set direction
    gpio_set_level(DIR_GPIO, step_direction);

    //Set step size
    gpio_set_level(USM0_GPIO, USM0);
    gpio_set_level(USM1_GPIO, USM1);

    //step once

    //set step high
    gpio_set_level(STEP_GPIO, 1);
    //set pulse size (1 = 1ms)
    vTaskDelay(pulse / portTICK_PERIOD_MS);
    
    //set step low
    gpio_set_level(STEP_GPIO, 0);
    //set pulse size (1000 = 1s)
    vTaskDelay(pulse / portTICK_PERIOD_MS);

}


int check_poles(KeyValuePair* revAbsDict) {

    //initialize variables
    int new_rssi = 0;
    int total_n_strength = 0;
    int total_s_strength = 0;
    int total_e_strength = 0;
    int total_w_strength = 0;

    //check rssi at 4 poles 3 times
    for (int i = 0; i < 3; i++) 
    {
        //get rssi at north
        vTaskDelay(RSSI_WAIT_TIME / portTICK_PERIOD_MS);
        //!!!get rssi value function here!!!
        new_rssi = getValueForKey(0.000, revAbsDict);
        Serial.print("Value for key ");
        Serial.print(0.000, 3);
        Serial.print(": ");
        Serial.println(new_rssi);
        //!!!get rssi value function here!!!
        total_n_strength = total_n_strength + new_rssi;

        //move to east and get rssi
        for (int i = 0; i < 50; i++) 
        {
            step(1, 40, 0, 0);
        }
        vTaskDelay(RSSI_WAIT_TIME / portTICK_PERIOD_MS);
        //!!!get rssi value function here!!!
        new_rssi = getValueForKey(90.000, revAbsDict);
        Serial.print("Value for key ");
        Serial.print(90.000, 3);
        Serial.print(": ");
        Serial.println(new_rssi);
        //!!!get rssi value function here!!!
        total_e_strength = total_e_strength + new_rssi;

        //move to south and get rssi
        for (int i = 0; i < 50; i++) 
        {
            step(1, 40, 0, 0);
        }
        vTaskDelay(RSSI_WAIT_TIME / portTICK_PERIOD_MS);
        //!!!get rssi value function here!!!
        new_rssi = getValueForKey(180.000, revAbsDict);
        Serial.print("Value for key ");
        Serial.print(180.000, 3);
        Serial.print(": ");
        Serial.println(new_rssi);
        //!!!get rssi value function here!!!
        total_s_strength = total_s_strength + new_rssi;

        //move to west and get rssi
        for (int i = 0; i < 50; i++) 
        {
            step(1, 40, 0, 0);
        }
        vTaskDelay(RSSI_WAIT_TIME / portTICK_PERIOD_MS);
        //!!!get rssi value function here!!!
        new_rssi = getValueForKey(270.000, revAbsDict);
        Serial.print("Value for key ");
        Serial.print(270.000, 3);
        Serial.print(": ");
        Serial.println(new_rssi);
        //!!!get rssi value function here!!!
        total_w_strength = total_w_strength + new_rssi;

        //move back to north
        for (int i = 0; i < 150; i++) 
        {
            step(0, 40, 0, 0);
        }
    }

    if ((total_n_strength < total_e_strength) && (total_n_strength < total_s_strength) && (total_n_strength < total_w_strength)) {
        return 0;
    }
    else if ((total_e_strength < total_s_strength) && (total_e_strength < total_w_strength)) {
        return 1;
    }
    else if (total_s_strength < total_w_strength) {
        return 2;
    }
    else if (total_w_strength < total_s_strength) {
        return 3;
    }
    else {
        return 4;
    }

}

void setup() {
  // put your setup code here, to run once:
  Serial.begin(9600); 
  // Setup UART
  // UART1, Pycom
  MySerial1.begin(9600, SERIAL_8N1, RX1, TX1);
  // UART2, XBEE
  MySerial2.begin(9600, SERIAL_8N1, RX2, TX2);
  KeyValuePair* revAbsDict = new KeyValuePair[DICT_SIZE];
  //change the 181.125 to the angle you want it to be
  createRevAbsDict(292.5, revAbsDict);
}

void loop() {
  KeyValuePair* revAbsDict = new KeyValuePair[DICT_SIZE];
  //change the 181.125 to the angle you want it to be
  createRevAbsDict(292.5, revAbsDict);

  PycomReceived1 = MySerial1.readStringUntil('\r'); 
  // System does not start until "start signal" is sent
  if (PycomReceived1 == "esp32 check "){
    Serial.println("RECEIVED");

      //Configure GPIO pin directions
      gpio_set_direction(STEP_GPIO, GPIO_MODE_OUTPUT);
      gpio_set_direction(DIR_GPIO, GPIO_MODE_OUTPUT);
      gpio_set_direction(RESET_GPIO, GPIO_MODE_OUTPUT);
      gpio_set_direction(USM0_GPIO, GPIO_MODE_OUTPUT);
      gpio_set_direction(USM1_GPIO, GPIO_MODE_OUTPUT);
      gpio_set_direction(HOMEN_GPIO, GPIO_MODE_INPUT);

      //initialize variables
      bool j;
      int pole;
      int num_full_step;
      int num_eighth_step;
      int current_rssi;
      int best_rssi;
      float current_angle; // holds the value of the angle from north the motor is facing at any given time
      float best_angle;  
      float transmitter_direction; // degrees from north that the signal is coming from
      
      //Set reset to high so it can work
      gpio_set_level(RESET_GPIO, 1);

      //number of full steps to take per point when sweeping
      num_full_step = ((SWEEP_ANGLE / (SWEEP_STEP_COUNT - 1)) / 1.8);

      //number of eigth steps to take per point when sweeping
      num_eighth_step = (((SWEEP_ANGLE / (SWEEP_STEP_COUNT - 1)) - (num_full_step * 1.8)) / 0.225);

      current_angle = 0;
      best_rssi = 10000;
      j = 0;
      while (j == 0) {

          //run the check poles function to find which pole has strongest signal
          pole = check_poles(revAbsDict);

          //scan around the pole with strongest signal or rerun check poles
          if (pole == 0) {
              //north is best, scan around it

              //move left of pole (sweep angle / 2) degrees
              for (int i = 0; i < (SWEEP_ANGLE / 3.6); i++) 
              {
                  step(0, 40, 0, 0);
                  current_angle = current_angle - 1.8;
              }

              //SWEEP

              //get first point
              vTaskDelay(RSSI_WAIT_TIME / portTICK_PERIOD_MS);

              //!!!get rssi value function here!!!
              current_rssi = getValueForKey(current_angle, revAbsDict);
              Serial.print("Value for key ");
              Serial.print(current_angle, 3);
              Serial.print(": ");
              Serial.println(current_rssi);
              if (current_rssi < best_rssi ) {
                  best_rssi = current_rssi;
                  best_angle = current_angle;
              }
              //!!!get rssi value function here!!!

              for (int i = 0; i < (SWEEP_STEP_COUNT - 1); i++) { //SWEEP_STEP_COUNT - 1 = amount of points more to take 

                  //move to next point
                  for (int j = 0; j < num_full_step; j++) 
                  {
                      step(1, 40, 0, 0);
                      current_angle = current_angle + 1.8;
                  }
                  for (int j = 0; j < num_eighth_step; j++) 
                  {
                      step(1, 40, 1, 1);
                      current_angle = current_angle + 0.225;
                  }

                  //record rssi at that point
                  vTaskDelay(RSSI_WAIT_TIME / portTICK_PERIOD_MS);

                  //!!!get rssi value function here!!!
                  current_rssi = getValueForKey(current_angle, revAbsDict);
                  if (current_rssi < best_rssi ) {
                      best_rssi = current_rssi;
                      best_angle = current_angle;
                  }
                  //!!!get rssi value function here!!!
                  
              }
              
              //move back to north

              //walk back the sweep (same for all poles)
              for (int i = 0; i < ((num_full_step)*(SWEEP_STEP_COUNT - 1)); i++) 
              {
                  step(0,40,0,0);
                  current_angle = current_angle - 1.8;
              }
              for (int i = 0; i < ((num_eighth_step)*(SWEEP_STEP_COUNT - 1)); i++) 
              {
                  step(0,40,1,1);
                  current_angle = current_angle - 0.225;
              }

              //walk from left edge of sweep to north (depending on the pole) 
              for (int i = 0; i < (SWEEP_ANGLE / 3.6); i++) 
              {
                  step(1, 40, 0, 0);
                  current_angle = current_angle + 1.8;
              }

              //set transmitter direction at angle of strongest signal
              transmitter_direction = best_angle;


              //exit while loop
              j = 1;
          }
          else if (pole == 1) {
              //east is best, scan around it

              //move to east
              for (int i = 0; i < 50; i++) 
              {
                  step(1, 40, 0, 0);
                  current_angle = current_angle + 1.8;
              }


              //move left of pole (sweep angle / 2) degrees
              for (int i = 0; i < (SWEEP_ANGLE / 3.6); i++) 
              {
                  step(0, 40, 0, 0);
                  current_angle = current_angle - 1.8;
              }

              //SWEEP

              //get first point
              vTaskDelay(RSSI_WAIT_TIME / portTICK_PERIOD_MS);
              
              //!!!get rssi value function here!!!
              current_rssi = getValueForKey(current_angle, revAbsDict);
              Serial.print("Value for key ");
              Serial.print(current_angle, 3);
              Serial.print(": ");
              Serial.println(current_rssi);
              if (current_rssi < best_rssi ) {
                  best_rssi = current_rssi;
                  best_angle = current_angle;
              }
              //!!!get rssi value function here!!!

              for (int i = 0; i < (SWEEP_STEP_COUNT - 1); i++) { //SWEEP_STEP_COUNT - 1 = amount of points more to take 

                  //move to next point
                  for (int j = 0; j < num_full_step; j++) 
                  {
                      step(1, 40, 0, 0);
                      current_angle = current_angle + 1.8;
                  }
                  for (int j = 0; j < num_eighth_step; j++) 
                  {
                      step(1, 40, 1, 1);
                      current_angle = current_angle + 0.225;
                  }

                  //record rssi at that point
                  vTaskDelay(RSSI_WAIT_TIME / portTICK_PERIOD_MS);

                  //!!!get rssi value function here!!!
                  current_rssi = getValueForKey(current_angle, revAbsDict);
                  if (current_rssi < best_rssi ) {
                      best_rssi = current_rssi;
                      best_angle = current_angle;
                  }
                  //!!!get rssi value function here!!!
                  
              }
              
              //move back to north

              //walk back the sweep (same for all poles)
              for (int i = 0; i < ((num_full_step)*(SWEEP_STEP_COUNT - 1)); i++) 
              {
                  step(0,40,0,0);
                  current_angle = current_angle - 1.8;
              }
              for (int i = 0; i < ((num_eighth_step)*(SWEEP_STEP_COUNT - 1)); i++) 
              {
                  step(0,40,1,1);
                  current_angle = current_angle - 0.225;
              }

              //walk from left edge of sweep to center of pole (same for all poles)
              for (int i = 0; i < (SWEEP_ANGLE / 3.6); i++) 
              {
                  step(1, 40, 0, 0);
                  current_angle = current_angle + 1.8;
              }

              //move to north from east
              for (int i = 0; i < 50; i++) 
              {
                  step(0, 40, 0, 0);
                  current_angle = current_angle - 1.8;
              }


              //set transmitter direction at angle of strongest signal
              transmitter_direction = best_angle;

              //exit while loop
              j = 1;
          }
          else if (pole == 2) {
              //south is best, scan around it

              //move to south
              for (int i = 0; i < 100; i++) 
              {
                  step(1, 40, 0, 0);
                  current_angle = current_angle + 1.8;
              }


              //move left of pole (sweep angle / 2) degrees
              for (int i = 0; i < (SWEEP_ANGLE / 3.6); i++) 
              {
                  step(0, 40, 0, 0);
                  current_angle = current_angle - 1.8;
              }

              //SWEEP

              //get first point
              vTaskDelay(RSSI_WAIT_TIME / portTICK_PERIOD_MS);

              //!!!get rssi value function here!!!
              current_rssi = getValueForKey(current_angle, revAbsDict);
              Serial.print("Value for key ");
              Serial.print(current_angle, 3);
              Serial.print(": ");
              Serial.println(current_rssi);
              if (current_rssi < best_rssi ) {
                  best_rssi = current_rssi;
                  best_angle = current_angle;
              }
              //!!!get rssi value function here!!!

              for (int i = 0; i < (SWEEP_STEP_COUNT - 1); i++) { //SWEEP_STEP_COUNT - 1 = amount of points more to take 

                  //move to next point
                  for (int j = 0; j < num_full_step; j++) 
                  {
                      step(1, 40, 0, 0);
                      current_angle = current_angle + 1.8;
                  }
                  for (int j = 0; j < num_eighth_step; j++) 
                  {
                      step(1, 40, 1, 1);
                      current_angle = current_angle + 0.225;
                  }

                  //record rssi at that point
                  vTaskDelay(RSSI_WAIT_TIME / portTICK_PERIOD_MS);

                  //!!!get rssi value function here!!!
                  current_rssi = getValueForKey(current_angle, revAbsDict);
                  if (current_rssi < best_rssi ) {
                      best_rssi = current_rssi;
                      best_angle = current_angle;
                  }
                  //!!!get rssi value function here!!!
                  
              }
              
              //move back to north

              //walk back the sweep (same for all poles)
              for (int i = 0; i < ((num_full_step)*(SWEEP_STEP_COUNT - 1)); i++) 
              {
                  step(0,40,0,0);
                  current_angle = current_angle - 1.8;
              }
              for (int i = 0; i < ((num_eighth_step)*(SWEEP_STEP_COUNT - 1)); i++) 
              {
                  step(0,40,1,1);
                  current_angle = current_angle - 0.225;
              }

              //walk from left edge of sweep to center of pole (same for all poles)
              for (int i = 0; i < (SWEEP_ANGLE / 3.6); i++) 
              {
                  step(1, 40, 0, 0);
                  current_angle = current_angle + 1.8;
              }

              //move to north from south
              for (int i = 0; i < 100; i++) 
              {
                  step(0, 40, 0, 0);
                  current_angle = current_angle - 1.8;
              }

              //set transmitter direction at angle of strongest signal
              transmitter_direction = best_angle;

              //exit while loop
              j = 1;
          }
          else if (pole == 3) {
              //west is best, scan around it

              //move to west
              for (int i = 0; i < 150; i++) 
              {
                  step(1, 40, 0, 0);
                  current_angle = current_angle + 1.8;
              }


              //move left of pole (sweep angle / 2) degrees
              for (int i = 0; i < (SWEEP_ANGLE / 3.6); i++) 
              {
                  step(0, 40, 0, 0);
                  current_angle = current_angle - 1.8;
              }

              //SWEEP

              //get first point
              vTaskDelay(RSSI_WAIT_TIME / portTICK_PERIOD_MS);

              //!!!get rssi value function here!!!
              current_rssi = getValueForKey(current_angle, revAbsDict);
              Serial.print("Value for key ");
              Serial.print(current_angle, 3);
              Serial.print(": ");
              Serial.println(current_rssi);
              if (current_rssi < best_rssi ) {
              best_rssi = current_rssi;
              best_angle = current_angle;
              }
              //!!!get rssi value function here!!!

              for (int i = 0; i < (SWEEP_STEP_COUNT - 1); i++) { //SWEEP_STEP_COUNT - 1 = amount of points more to take 

                  //move to next point
                  for (int j = 0; j < num_full_step; j++) 
                  {
                      step(1, 40, 0, 0);
                      current_angle = current_angle + 1.8;
                  }
                  for (int j = 0; j < num_eighth_step; j++) 
                  {
                      step(1, 40, 1, 1);
                      current_angle = current_angle + 0.225;
                  }

                  //record rssi at that point
                  vTaskDelay(RSSI_WAIT_TIME / portTICK_PERIOD_MS);

                  //!!!get rssi value function here!!!
                  current_rssi = get_rssi();
                  if (current_rssi < best_rssi ) {
                      best_rssi = current_rssi;
                      best_angle = current_angle;
                  }
                  //!!!get rssi value function here!!!
                  
              }
              
              // move back to north
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

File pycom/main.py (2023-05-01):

import time
import re

import machine
import utime
from machine import UART
from network import WLAN
#https://github.com/nakagami/micropg Open source library for Postgres Database driver
import micropg
import pycom

pycom.heartbeat(False)
#Function to parse the time tuple in the database
def parse_tuple(input_string):
    input_string = input_string.strip("()")
    elements = input_string.split(", ")

    result = []
    for element in elements:
        if element == "None":
            result.append(None)
        else:
            result.append(int(element))

    return tuple(result)

#Connect and reconnect functions for WiFi
def connect_to_wifi(wlan, ssid):
    wlan.init(mode=WLAN.STA, ssid=ssid)
    wlan.connect(ssid=ssid, timeout=10000)
    while not wlan.isconnected():
        print("Trying to connect...")
        machine.idle()
    print("WiFi connected successfully")
    print(wlan.ifconfig())

def scan_and_connect(wlan, target_ssid):
    wlan.init(mode=WLAN.STA)
    while True:
        try:
            nets = wlan.scan()
            break
        except:
            time.sleep(3)
            pass
    for net in nets:
        if net.ssid == target_ssid:
            print('Network found!')
            wlan.connect(net.ssid, timeout=15000)
            while not wlan.isconnected():
                #machine.idle()  # save power while waiting
                print("Attempting connection...")
                time.sleep(1)
            print('WLAN connection succeeded!')
            break

def check_and_reconnect(wlan, target_ssid):
    while True:
        if wlan.isconnected():
            time.sleep(1)
            print("Connected!")
        else:
            print("Disconnected")
            time.sleep(3)
            scan_and_connect(wlan, target_ssid)

#Regex to check valid format
def is_valid_format(msg):
    #pattern = r'^\d{2}\.\d{6},-\d{2}\.\d{6}$'
    pattern = r"^\d{4}-\d{2}-\d{2} \d{2}:\d{2}:\d{2}\.\d+$"
    match = re.match(pattern, msg)
    return re.match(pattern, msg) is not None

#Constantly checking database to see if the value is 1
def wait_for_start_value():
    start_value_found = False

    while not start_value_found:
        cur.execute("SELECT * FROM start WHERE id = 1")

        result = cur.fetchone()
        

        if result:
            start_value_found = True
            print("Start button pressed, begginning update")

            cur.execute("UPDATE start SET id = 0")
            conn.commit()
            return
        else:
            time.sleep(1)



#Performing update if the time is different than the built in time 
def update_row_if_time_different(recname, new_rec_lat, new_rec_long, new_trans_lat, new_trans_long, new_sig_angle, conn, cur):
    rtc=machine.RTC()
    rtc.ntp_sync("pool.ntp.org")

    current_time = rtc.now()

    current_time = utime.mktime(current_time)


    cur.execute("SELECT * FROM recdata2 WHERE recname = %s", (recname,))

    row = cur.fetchone()


    if row:
        last_updated_time = row[6]

        if is_valid_format(last_updated_time):

            date_parts, time_parts = last_updated_time.split(" ")
            year, month, day = [int(x) for x in date_parts.split("-")]
            hour_str, minute_str, second_parts = time_parts.split(":")
            hour, minute = int(hour_str), int(minute_str)
            second, microsecond = [int(x) for x in second_parts.split(".")]

            time_tuple = (year, month, day, hour, minute, second, microsecond, None)

            last_updated_time = utime.mktime(time_tuple)
        else:

            time_tuple = parse_tuple(last_updated_time)
            last_updated_time = utime.mktime(time_tuple)

        if last_updated_time != current_time:

            cur.execute("""
                UPDATE recdata2
                SET rec_lat = %s, rec_long = %s, trans_lat = %s, trans_long = %s, sig_angle = %s, time_last_updated = %s
                WHERE recname = %s
            """, (new_rec_lat, new_rec_long, new_trans_lat, new_trans_long, new_sig_angle, str(time_tuple), recname))

            conn.commit()
#Function to send UART to ESP32 and then wait for data back        
def update_gui(conn, cur):

    while True:
        print("running")
        # P21 = G12 = Tx connects to GPIO 18 = Rx
        # PIN 6 IS RX for DEMO
        # PIN 5 IS TX for DEMO
        uart = UART(1, baudrate=9600, pins=('P5','P6'))
        strMsg = ''
        uart.write('esp32 check \r')
        time.sleep(1)
        if uart.any() >0:
            strMsg = uart.read().decode('utf-8')

            split_values = strMsg.split(',')

            if len(split_values) == 6:
                rec_name = float(split_values[0])
                rec_lat = float(split_values[1])
                rec_long = float(split_values[2])
                trans_lat = float(split_values[3])
                trans_long = float(split_values[4])
                sig_angle = float(split_values[5])

                
                update_row_if_time_different(rec_name, rec_lat, rec_long, trans_lat, trans_long, sig_angle, conn, cur)
                break
                
            else:
                print("not correct length in message")
            
        else:
            strMsg = "No data"
            print(strMsg)

#WiFi name
target_ssid = 'Verizon-SM-G930V-CD32'
wlan = WLAN()
pycom.rgbled(0x7f0000)
scan_and_connect(wlan, target_ssid)
pycom.rgbled(0x7f7f00)

#Creating Database connection
conn = micropg.connect(host='project403.c6uydewvrqoi.us-east-2.rds.amazonaws.com', port=5432, user='postgres',password='Nyhr7fv245', database='postgres', timeout=10000, use_ssl=False)
cur = conn.cursor()

pycom.rgbled(0x007f00)
print("Ready to press start")
wait_for_start_value()
pycom.rgbled(0x0000ff)
#Updating GUI
update_gui(conn, cur)
pycom.rgbled(0xff0000)
